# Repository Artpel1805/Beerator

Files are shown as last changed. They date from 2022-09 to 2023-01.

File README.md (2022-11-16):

# <div align="center">Beerator</div>
## Introduction

Le but du projet est de réaliser intégralement un robot capable de se déplacer, de chercher et d’attraper une canette (de bière ? 😶), relever sa couleur, puis de la déposer dans la zone de couleur correspondante.
Partant d’une liste de tous les composants principaux à employer et d’une proposition de châssis, toutes les étapes sont à réaliser de l’aspect matériel (Modélisation sous logiciel de CAO, soudage des composants) jusqu’à l’asservissement logiciel, en passant par la planification et la réalisation du PCB.

Voici un model 3D de ce à quoi pourrais ressembler le robot:

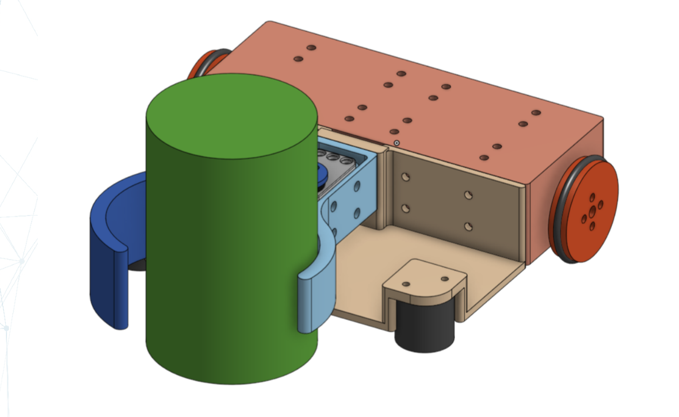
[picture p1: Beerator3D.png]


Le travail fut réparti entre les quatre membres de l’équipe, et les responsabilités suivantes furent attribuées:
* Chef de projet / Responsable intégration : Arthur Pellegrin
* Responsable Software : Nassim Rami
* Responsable Hardware : Adrien Lenoir
* Responsable Livrables : Clarisse Cheng

À l’écriture de ses lignes, nous avons planifié tout le projet, réalisé le PCB, designé et imprimé le châssis. Les composants sont en cours de soudage. Il reste ainsi à réaliser l’assemblage des pièces, l’algorithme de fonctionnement du robot, la commande des différents actionneurs, les calculs d’odométrie, et l’asservissement logiciel.

## General Informations

Vous trouverez dans ce repo bon nombre de dossier.

- Nous avons dans un premier temps rassembler les contraintes et les fonctionnalités du robot dans un cahier des charges: [Cahier des Charges](Cahier%20des%20Charges)

- Nous avons ensuite listé toutes les documentations des composants que nous utiliserons pour répondre à notre cahier des charges dans le dossier [Documentation](Documentation)

- Après cela nous avons architecturer la partie électronique du projet dans le dossier [Diagramme](Diagramme)

- Une fois l'architecture satisfaisante nous avons modéliser la carte électronique sous KiCaD vous trouverez le projet dans le dossier [KiCad/Beerator](KiCad/Beerator). Vous pourrez aussi trouver la BOM dans le fichier

- Nous avons en parallele esssayé d'améliorer le modele 3D du robot. Des choix ont été fait afin d'amméliorer la répartition des masses dans le robots et avoir une meilleure disposition des capteurs.

Les différents travaux effectués sont détaillés dans les parties qui suivent.

## Architecture du projet, schémas fonctionnels

### Architecture de la carte

Pour notre robot, nous proposons l'architecture suivante pour la carte:

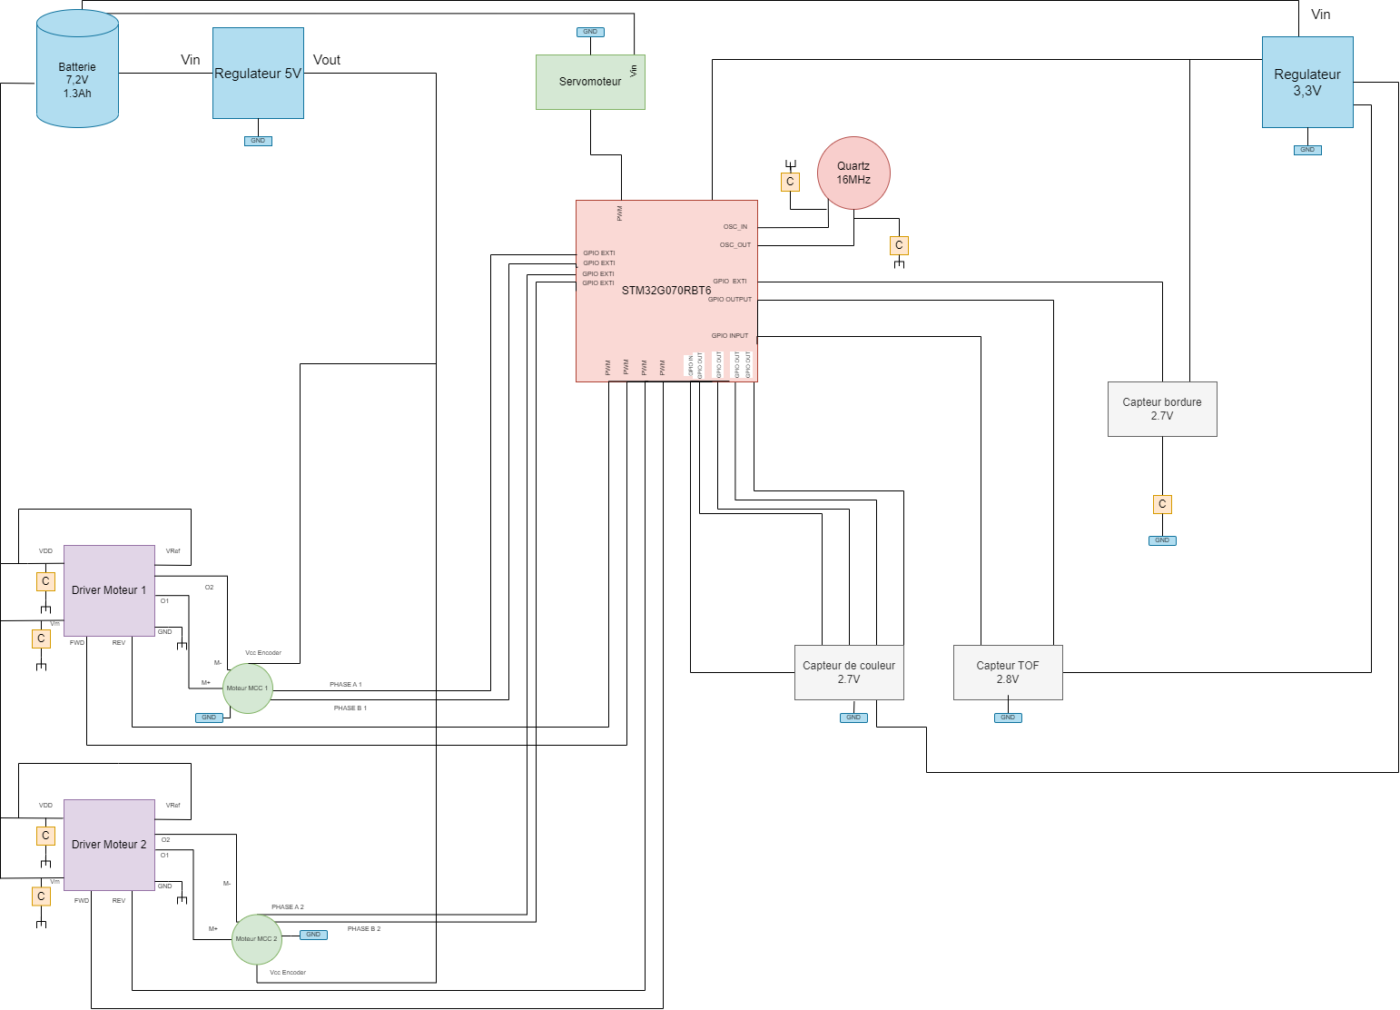
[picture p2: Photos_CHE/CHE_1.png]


Et pour les capteurs:

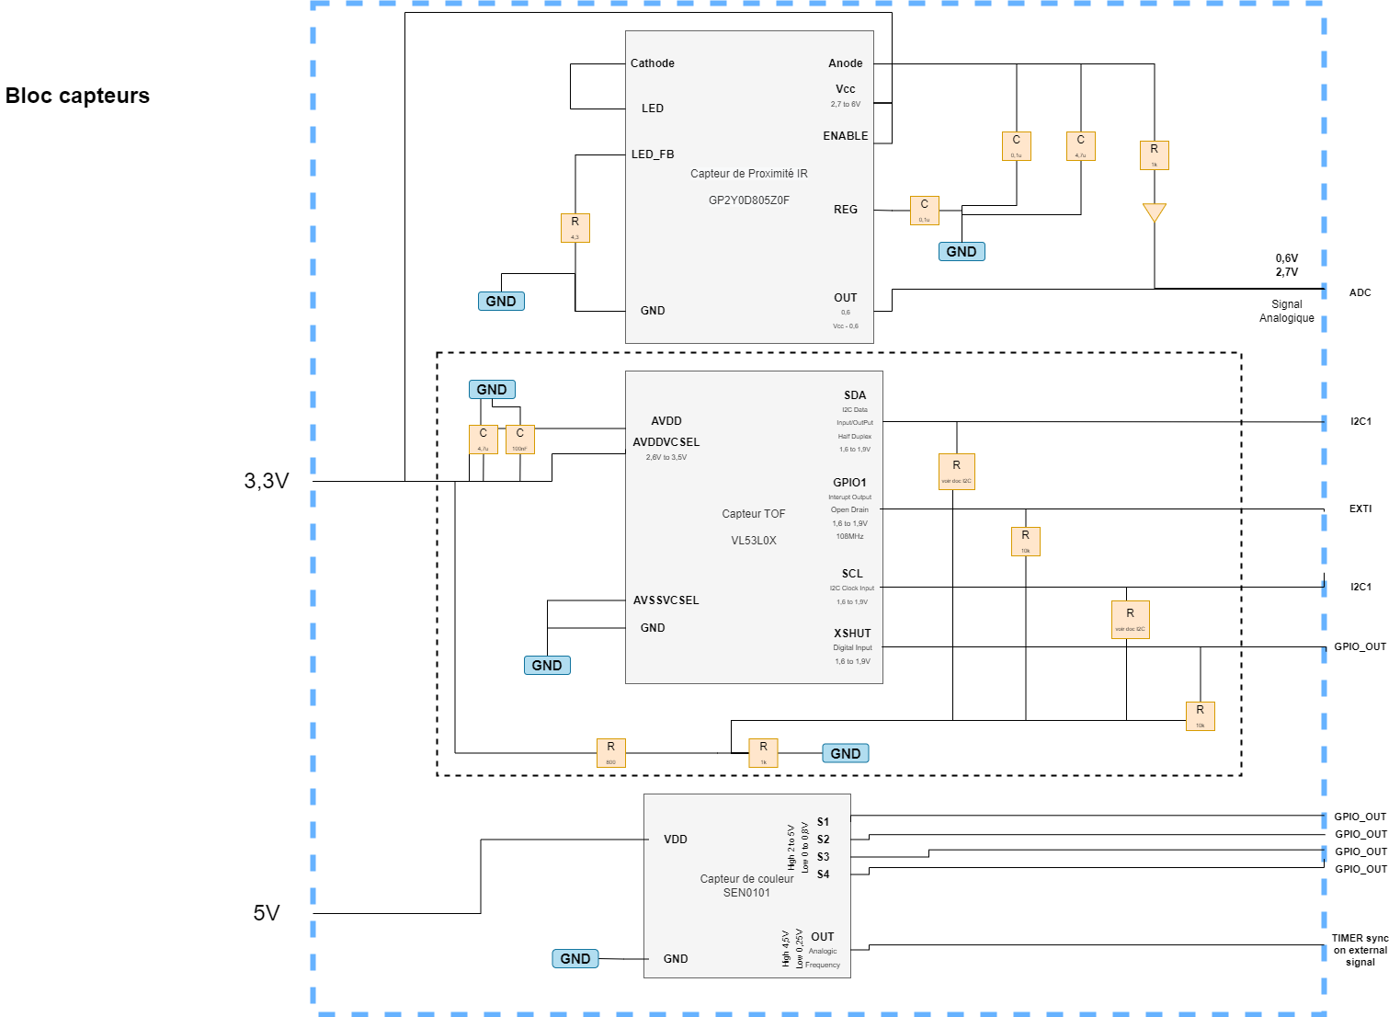
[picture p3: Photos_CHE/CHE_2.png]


* Les deux capteurs IR serviront à détecter les bordures, l’un sera placé à l’avant gauche du robot tandis que l’autre sera à l’avant droit. Ceci évitera au robot de tomber lorsque la distance entre la table et le robot sera supérieur à 5-10 cm environ. Ces deux capteurs IR sont respectivement connectés à une PIN de la STM32, un PIN ADC permettant de recueillir la distance à laquelle se situe la bordure. Le tout étant relié à un régulateur 3.3V permettant de contrôler l’intensité du courant et la tension de sortie.

* Le capteur TOF est connecté à 4 PIN du STM32 avec 2 connexions I2C, 1 EXTI et 1 GPIO OUT. Celui-ci nous permet de connaître la distance à laquelle se situent les canettes.

* Le capteur de couleur est équipé d'un oscillateur interne, oscillateur qui produit une onde carrée dont la fréquence est proportionnelle à l'intensité de la couleur. Fréquence qui nous permettra de déterminer la couleur de la canette. Ce capteur de couleur a une portée très, c’est pour cela que nous l’avons placer au creu de la pince.

* Quatre PWM seront utilisés pour contrôler le hacheur droit et gauche des moteurs

### Architecture de l’alimentation

Voici l’architecture de l’alimentation:

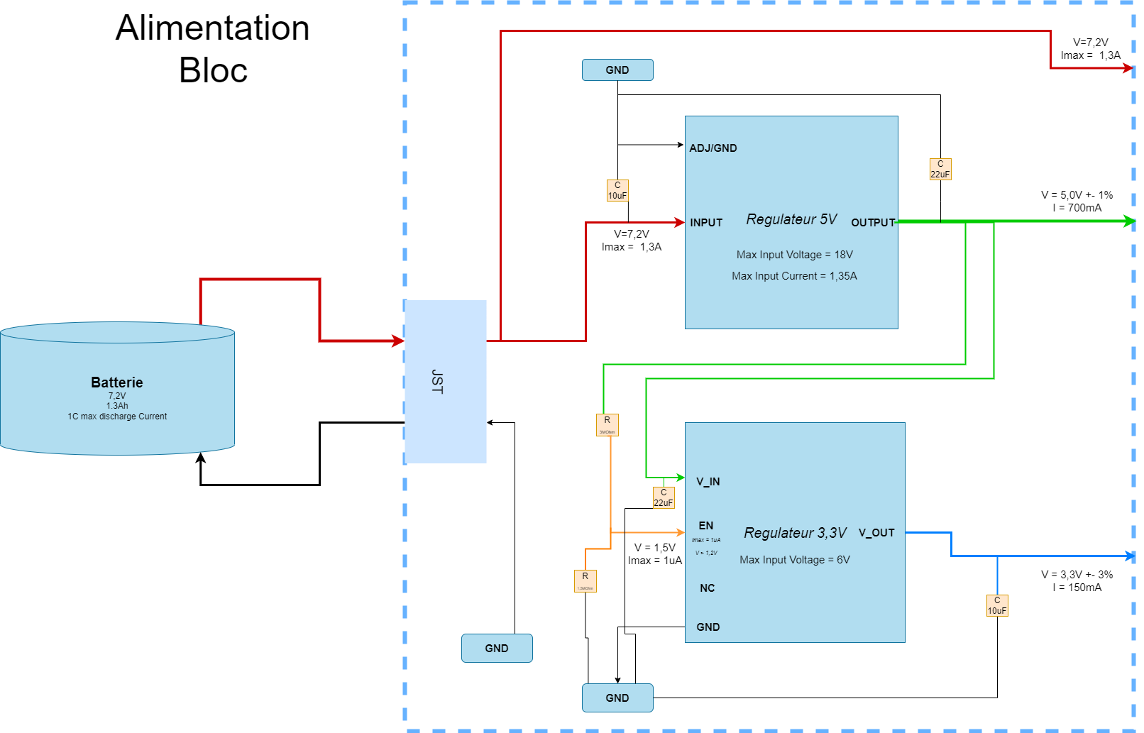
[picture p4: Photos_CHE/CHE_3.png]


Dans un premier temps, la batterie de 7.2V va nous permettre d’alimenter nos différents régulateurs qui vont à leur tour alimenter les composants de notre robot.

Les capteurs TOF et IR ont besoin d’une tension de maximale de 2.8V, on utilise donc un régulateur 3.3V pour abaisser la tension de l’alimentation. 
De même, pour le capteur de couleur, nous utilisons un régulateur 5V.

### Diagramme d’état

Voici le diagramme d’état du robot qui spécifie les réactions du robots à différents évènements qui pourraient avoir lieu. Le but du robot est d'abord de détecter la canette ou les canettes présente sur la table, pour se diriger vers elle, la saisir puis la déposer dans la zone qui correspond à sa couleur. Ces étapes sont développées dans le diagramme d’état ci-contre.

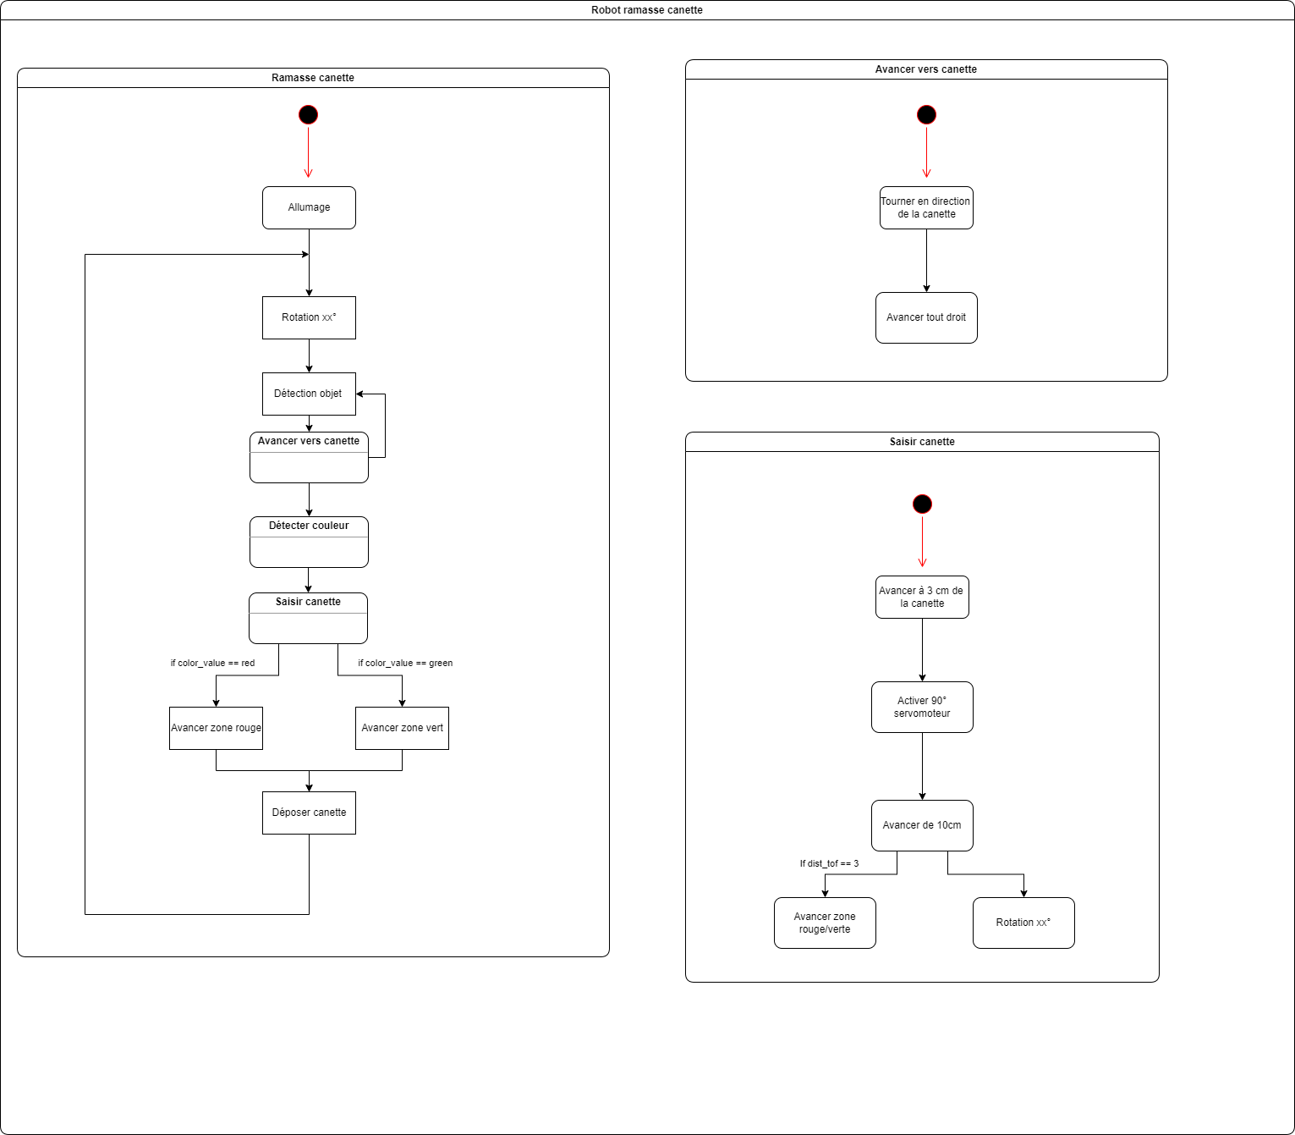
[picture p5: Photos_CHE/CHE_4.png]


## Planification du circuit, Création du PCB

Comme vu précédemment nous avons découpé l'électronique de notre robot en 4 blocs fonctionnels.

Nous devons maintenant créer le schéma électronique de notre carte en respectant cette répartition. Cela n’a pas d'effet sur l'électronique impliqué, mais cela aidera à la maintenabilité et à la lisibilité du projet.

De même, nous traitons chaque composant indépendamment. Ils seront reliés grâce à des labels dans le logiciel * KiCad *.

### ALIMENTATION

Nous avons décidé de connecter la batterie grâce à un JST, ainsi nous pourrons facilement la retirer pour la recharger.
Concernant les régulateurs, nous dimensionnons leurs capacités de découplage en accord avec leurs documentations respectives.

Nous avons ensuite décidé de rajouter des témoins d’alimentation sur la batterie et le 3.3V. Les leds que nous avons choisies consomment 10mA pour fournir une luminosité maximale.
Comme ce sont uniquement des témoins (Nous n’avons pas besoin de beaucoup de luminosité) et que le 3.3V ne peut pas fournir une trop grande intensité nous avons choisis de réduire le courant maximal à 1mA. 
Nous dimensionnons donc les résistances en conséquence, avec une loi d’ohm sachant que les LEDs sont en 3V. 

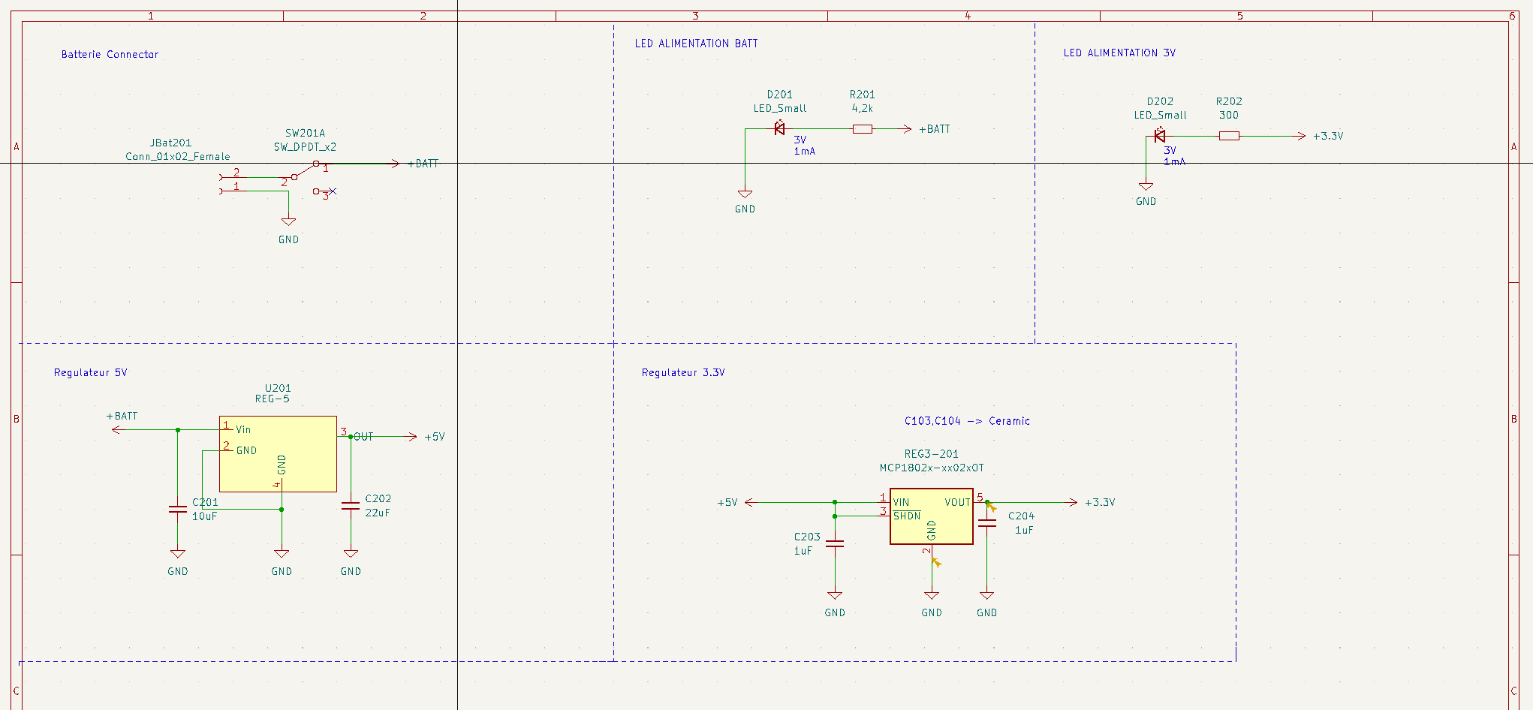
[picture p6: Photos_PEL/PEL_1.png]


### CAPTEURS

Nous avons décidé de connecter tous nos capteurs grâce à des JST. 
Cela permettra une meilleure modularité physique des capteurs sur le robot.
Cela évite aussi de concevoir une grande carte ou plusieurs cartes, les capteurs disposant presque tous de leur propre carte.

Nous avons quand même dû ici respecter la géométrie des capteurs afin que les JST correspondent aux bonnes I/O des cartes électroniques des capteurs.

Des résistances de Pull-Up ont dû être ajoutées, pour l’I2C car cela est nécessaire pour que ce protocole fonctionne correctement.

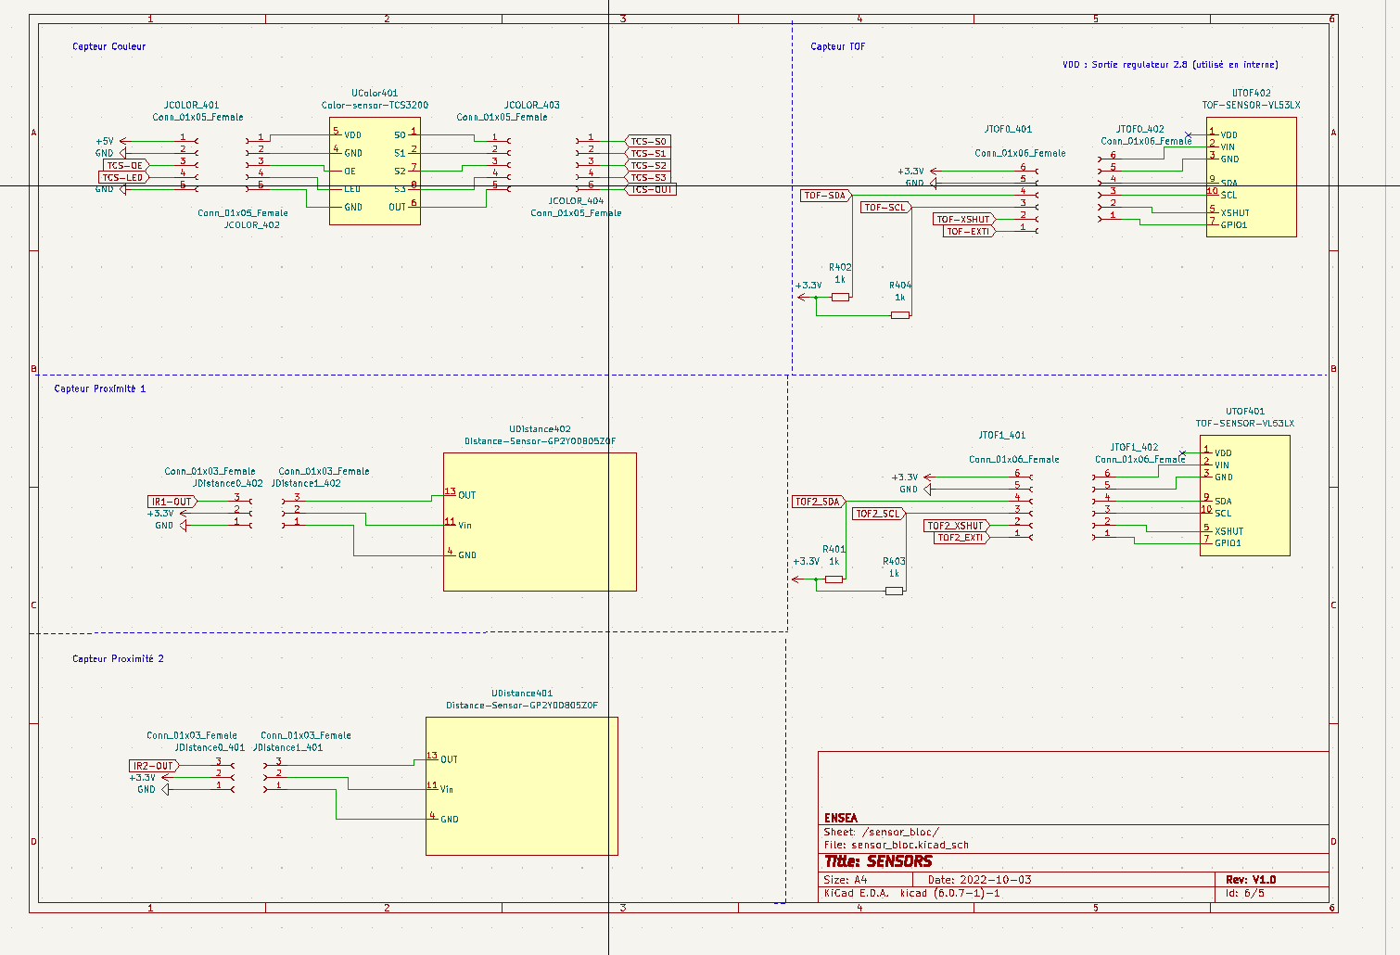
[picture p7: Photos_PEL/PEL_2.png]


### ACTIONNEURS

Nous avons 3 actionneurs - 2 MCC et 1 Servomoteur.

Les MCC sont commandés par des Drivers et leurs capacités de découplage.
Cette partie du projet est assez délicate. Nous décidons donc de mettre des Solder Jump afin de pouvoir tester nos signaux avant de les connecter aux moteurs.

Le Servo quant à lui suit un protocole particulier, il sera branché sur un port USART en mode Half-Duplex du uP nécessitant une résistance de Pull-Up.

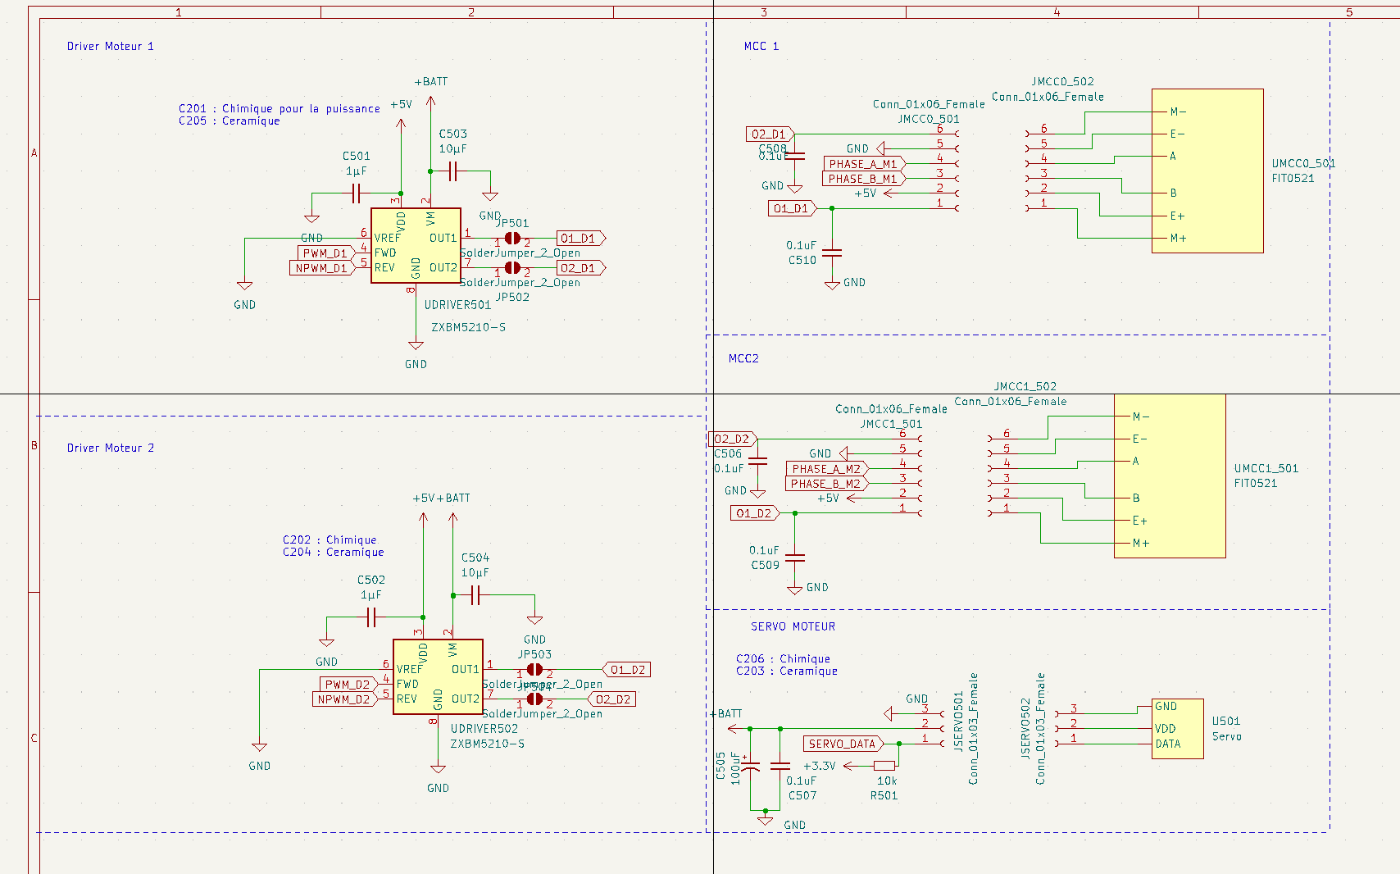
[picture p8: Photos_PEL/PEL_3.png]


### CONTRÔLEUR

Jusqu’ici tous les modèles électroniques et les placements de toutes les I/O étaient imposés par les constructeurs.

Nous modélisons le microcontrôleur avec ses 64 broches. 
Ensuite nous avons dû brancher tous nos composants à notre microcontrôleur.

Nous avons mis un point d’honneur à optimiser le choix des broches en suivant un protocole bien particulier: 
Regrouper au maximum les broches étant reliées à un même composant
Organiser les broches de manière à minimiser les croisements lors du routage
Segmenter les sous-circuits
Prendre en compte les problèmes de compatibilité électgromagnétique

Grâce au logiciel STM32CubeMx nous avons pu placer les broches sur des pins répondant aux besoins.

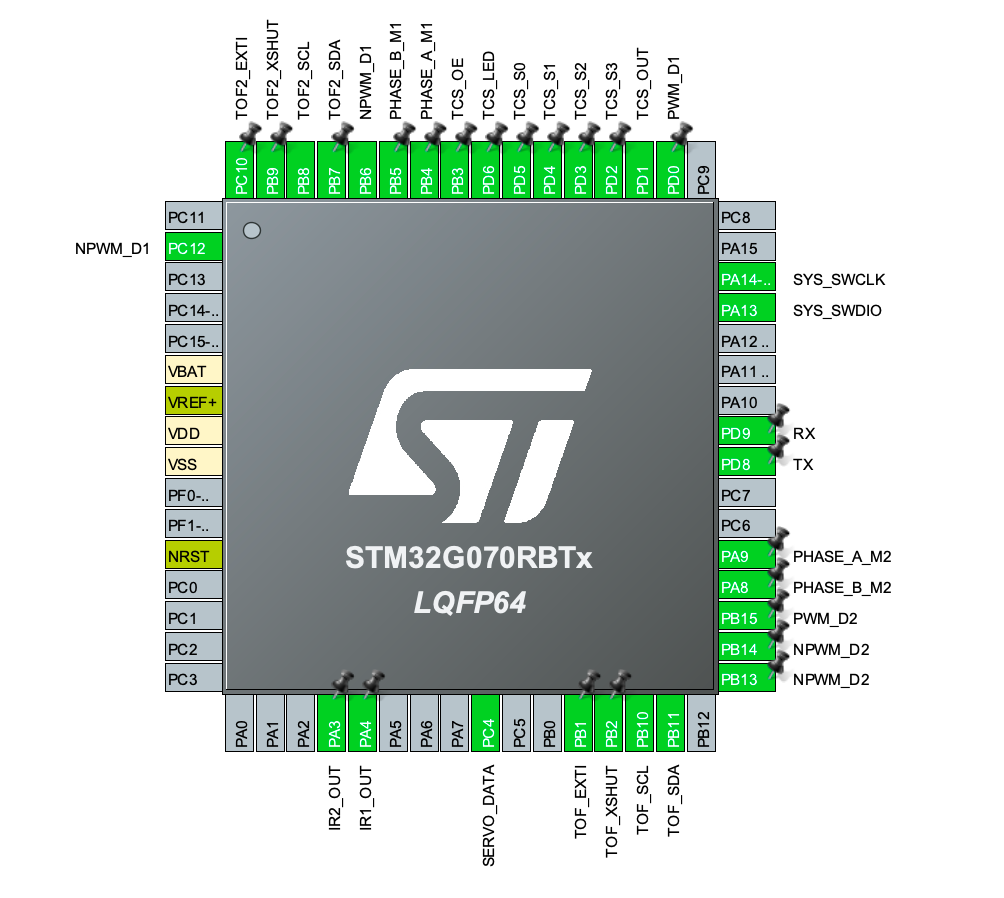
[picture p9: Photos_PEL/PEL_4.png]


Nous devons aussi alimenter le STM32 et il ne faut surtout pas oublier les capacités de découplage car l’alimentation doit être la plus stable possible.

Nous choisissons aussi de rajouter un Quartz externe, car l’horloge est plus précise.

Il ne faut pas oublier de rajouter, les branchements pour le STLink car c’est lui qui nous permettra de programmer le STM32.

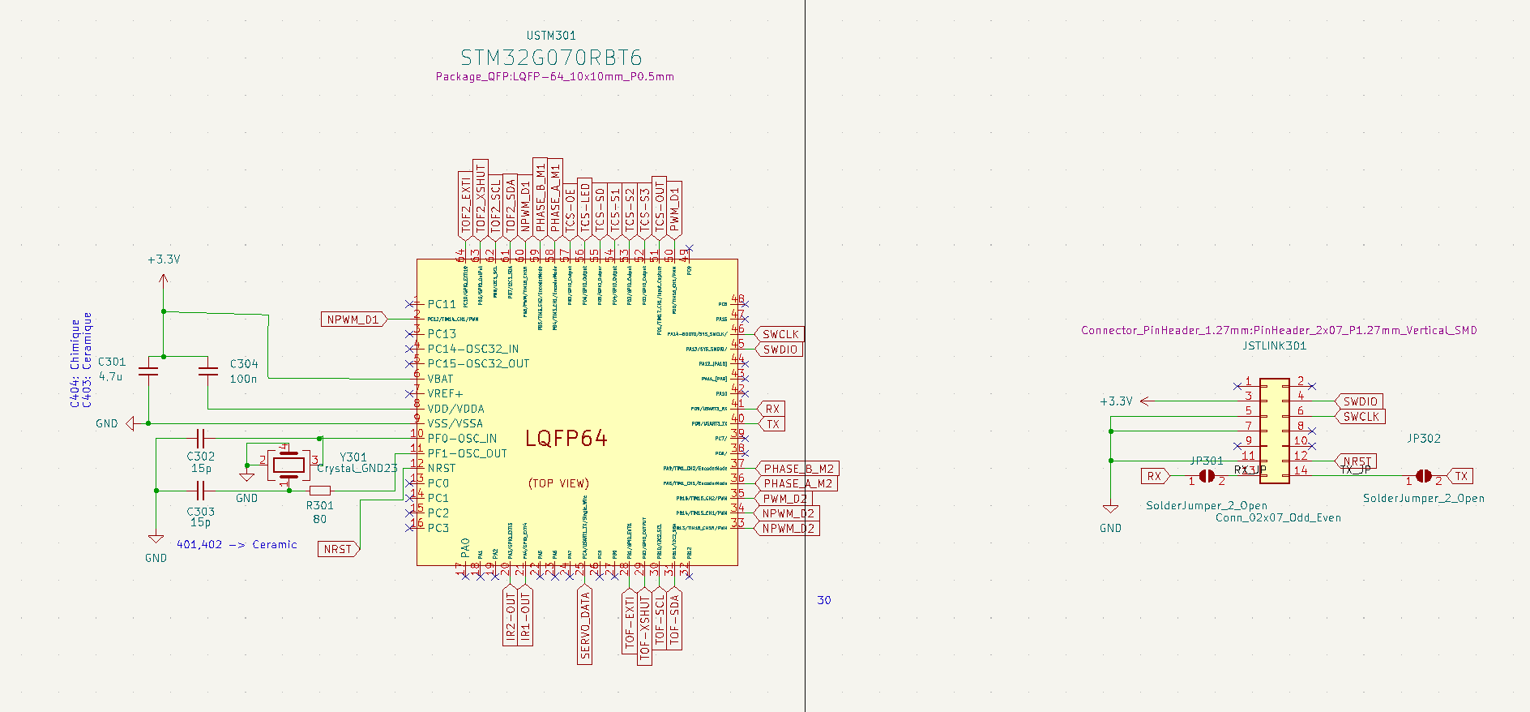
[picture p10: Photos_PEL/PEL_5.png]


Enfin nous réalisons une analyse électrique de notre circuit pour savoir s’il comporte des erreurs et nous les corrigeons jusqu’à ce qu’il n’y en ai plus.

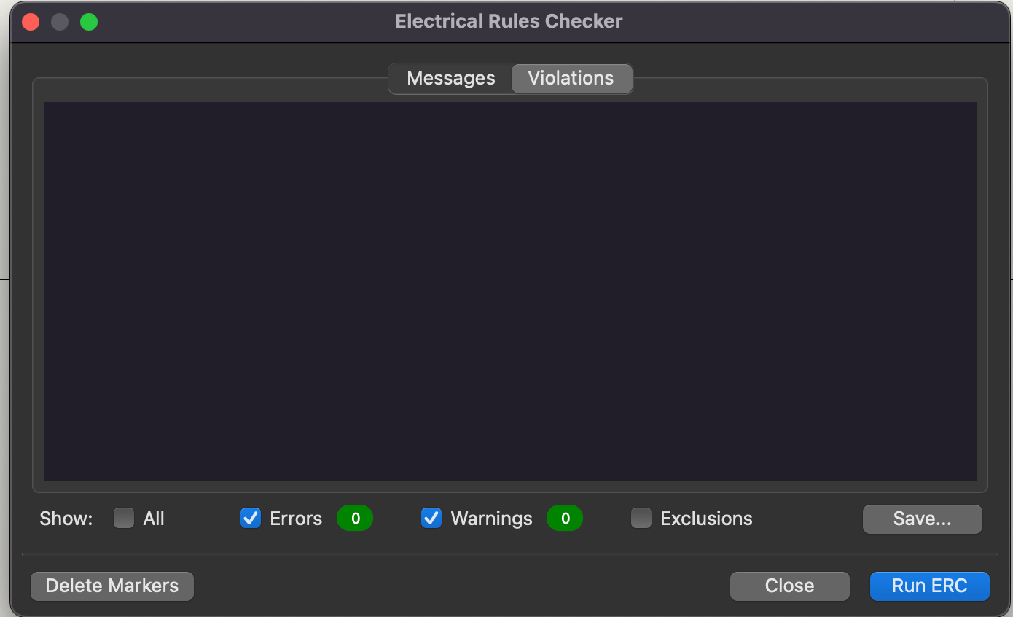
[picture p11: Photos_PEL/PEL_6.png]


### Production du PCB

La prochaine étape est d’assigner les empreintes correspondants aux composants. Nous utiliserons des composants SMD 0603. Pour les connecteurs nous avons utilisé des connecteurs JST de type JST HX 2.54mm.
On peut remarquer que certains composants ne sont pas assignés, en effet ce sont les composants qui seront directement soudé au capteur donc ils ne doivent pas être présent sur notre PCB

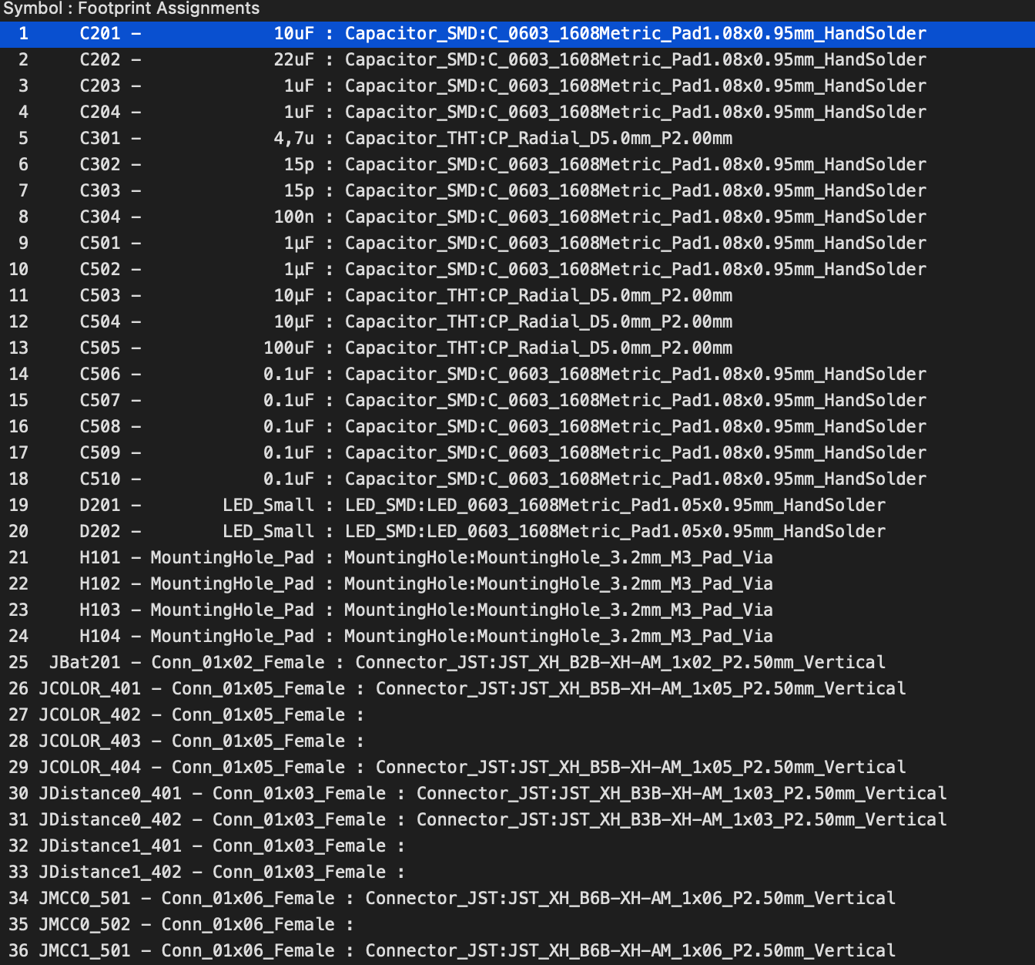
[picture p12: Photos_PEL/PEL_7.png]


Nous travaillons sur un PCB 4 couches, on décide donc d’y placer 2 plans de potentiels séparés par 2 plans de masses pour d'obscures raisons de CEM.
On peut voir ci dessous le Stack-Up de notre carte

* <font color=red>5V (Rouge)</font>
* <font color=green>GND (Vert)</font>
* <font color=yellow>3,3V (Jaune)</font>
* <font color=blue>GND (Bleu)</font>

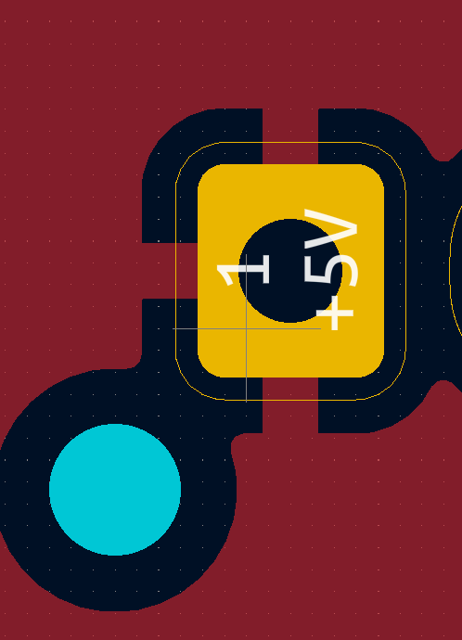
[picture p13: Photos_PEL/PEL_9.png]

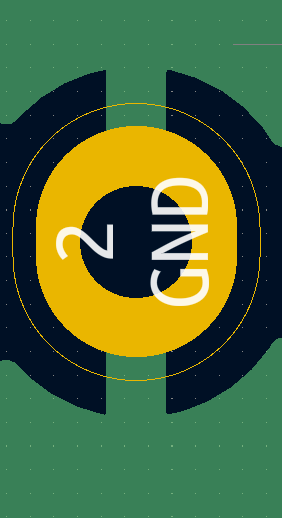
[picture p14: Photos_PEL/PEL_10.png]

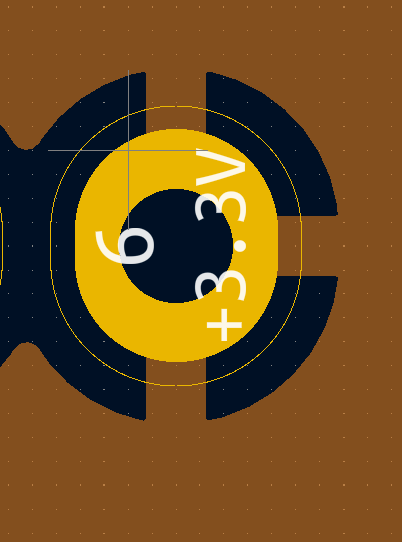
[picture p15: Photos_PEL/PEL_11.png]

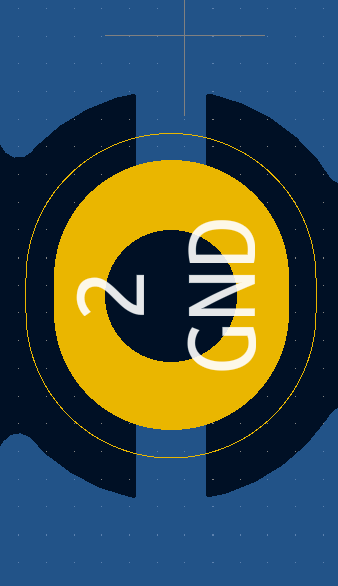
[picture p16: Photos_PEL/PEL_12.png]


JLC PCB, le fabricant de nos carte nous impose aussi des contraintes de conception que nous devons renseigner.

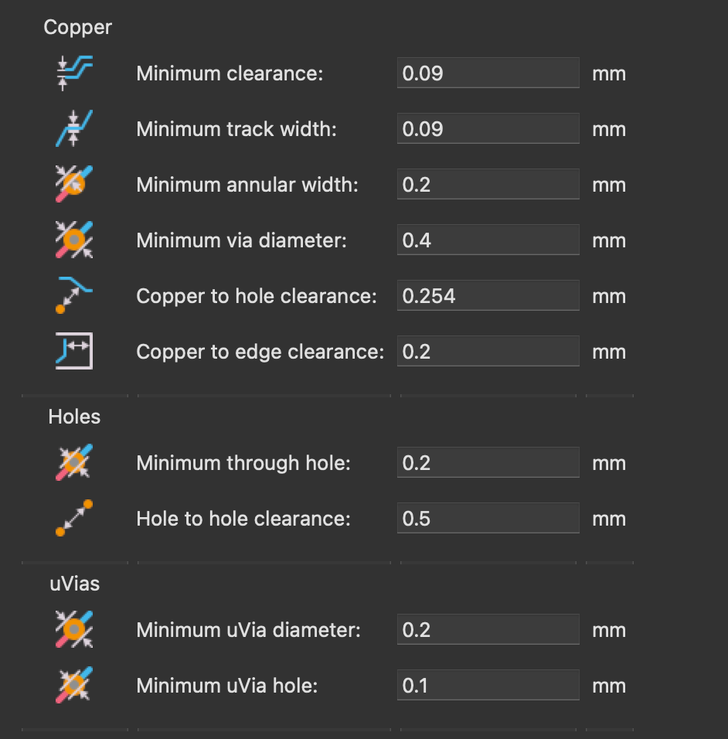
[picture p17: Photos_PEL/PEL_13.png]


La prochaine est le placement des composants sur le PCB.
Nous essayons de regrouper les composants au maximum par groupe pour que le routage soit le plus simple possible

On décide aussi de placer le STM32 au centre car c’est lui qui possède le plus de connexion.

On voit ci dessous en vert tous les composants relatif au contrôle, en rouge tous le bloc actionneurs, en bleu le bloc alimentation et en jaune le bloc capteur

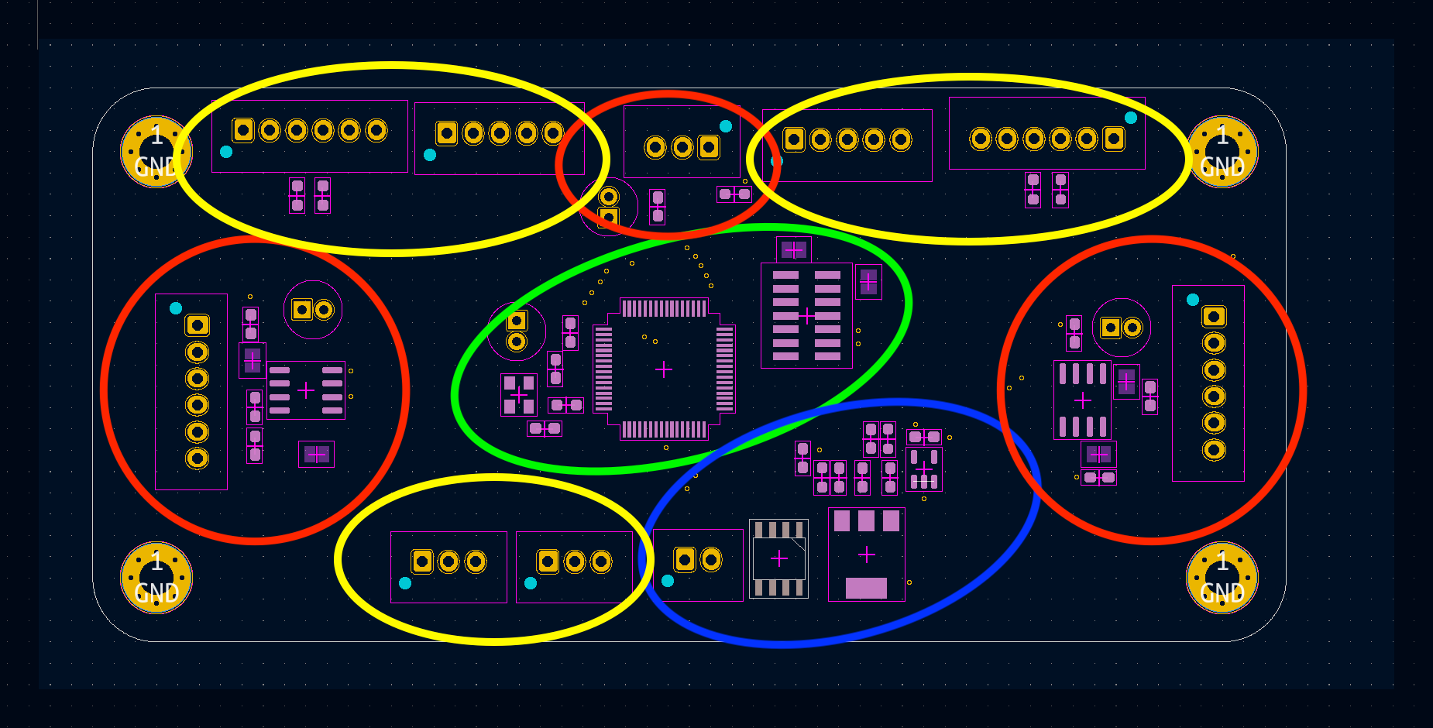
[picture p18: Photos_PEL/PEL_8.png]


Nous relions ensuite tous les composants électriquement. Nous veillerons aussi à utiliser les pistes les plus larges possible surtout pour la partie puissance. 
Cela permet de laisser passer le courant nécessaire et d’éviter des problèmes de CEM.

Quelques règles de CEM que nous nous efforçons de respecter : 
Pas d’angle à 90º
Les signaux à haute fréquence ne doivent pas se croiser, et les pistes doivent être le plus court possible
Il faut essayer de respecter une distance entre les pistes

Voici ce à quoi ressemblent nos deux plans avec des pistes.

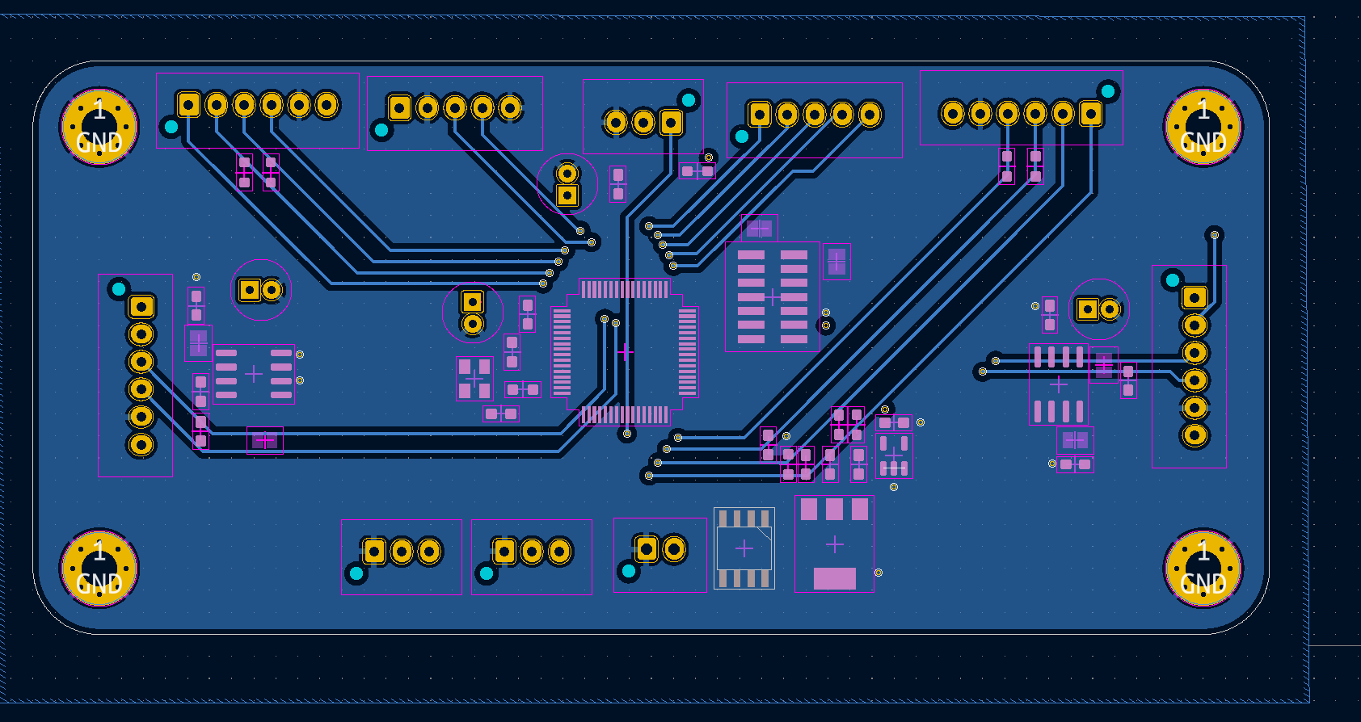
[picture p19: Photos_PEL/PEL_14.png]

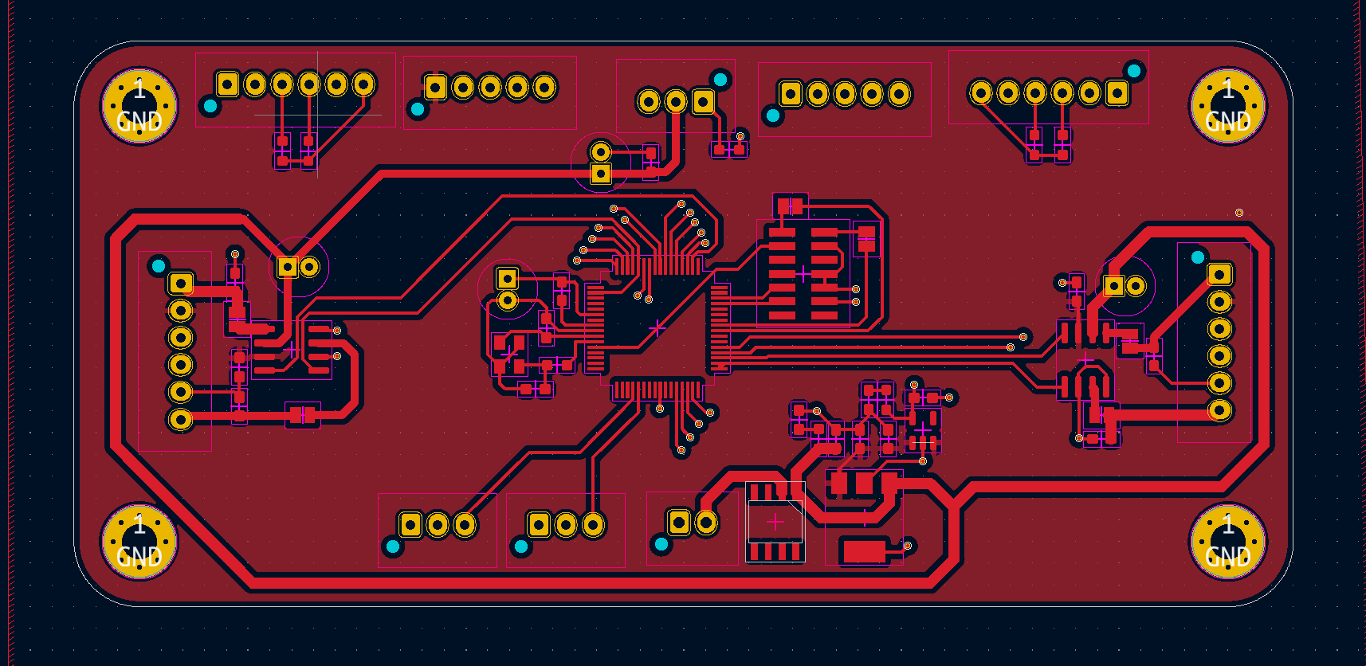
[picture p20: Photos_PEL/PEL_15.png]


Et enfin notre carte modélisé en 3D

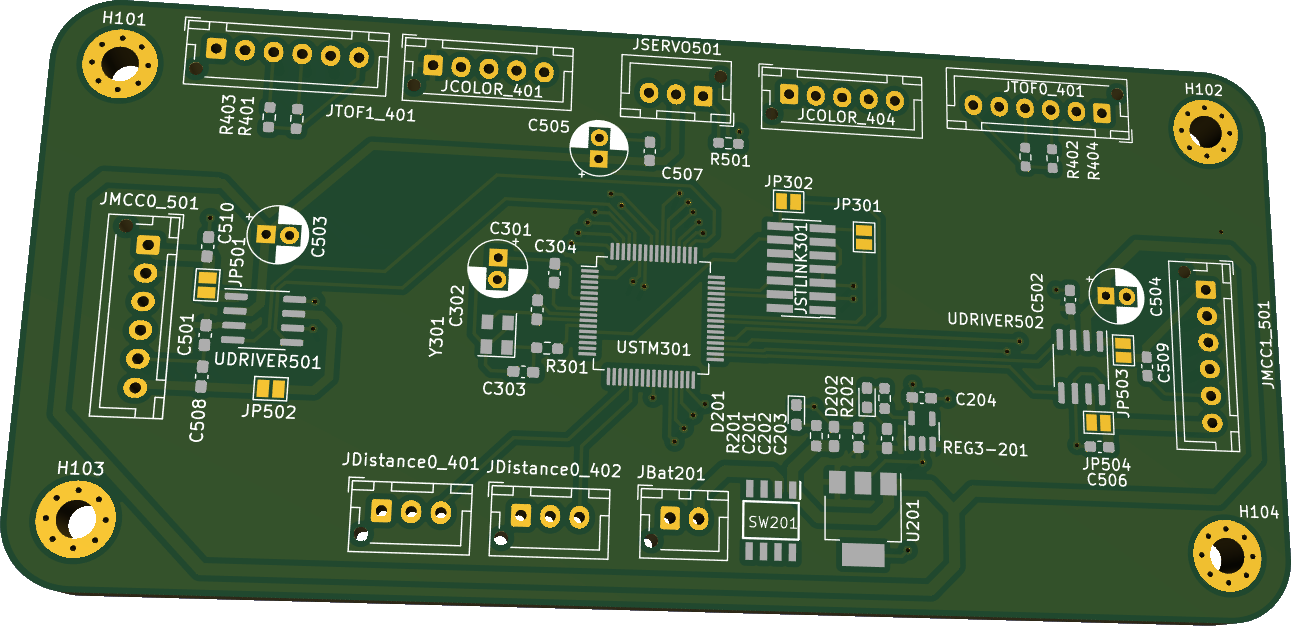
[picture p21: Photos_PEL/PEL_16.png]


## Capteurs, spécificités software

Dans cette partie, on se basera sur le choix des composants et leur protocole de communication ainsi que leur fonctionnalité pour atteindre les objectifs demandés par le cahier de charge afin que le robot puisse fonctionner correctement.

### TCS3200 - Capteur de Couleur

Le capteur VEML3328 détecte les couleurs rouge, le vert, le bleu en incorporant des photodiodes, des amplificateurs et des circuits analogiques/numériques dans une seule puce CMOS. Avec ce capteur, la luminosité et la température de couleur d'un rétroéclairage d'affichage peuvent être ajusté en fonction de la source de lumière ambiante, et il peutdifférencier les environnements d'éclairage intérieurs des environnements d'éclairage extérieurs.Il existe une relation entre la sortie et l'intensité lumineuse. La gamme de  sortie est typique de 2hz à 500Khz.
Ce dispositif utilise une liaison direct avec le microcontrôleur.
Puisque le diapositif nous fournit comme output un signal variant en fréquence , on a utilisé la fonction du Timer : Input capture mode , qui permet de détecter chaque front montant et en calculant la différence on peut avoir la fréquence.

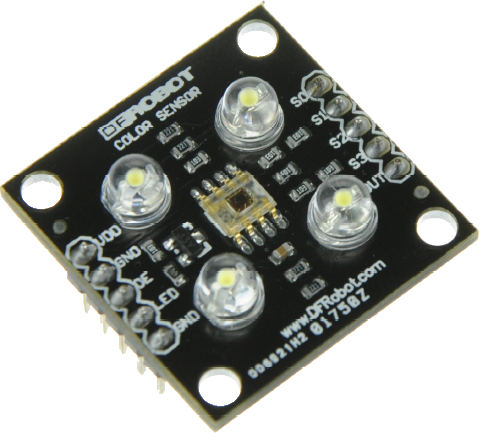
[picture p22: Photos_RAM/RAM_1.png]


#### Calibration

Pour calibrer le capteur, nous avons besoin d'un objet blanc.On place un objet blanc près du capteur. Après le calibrage, si on garde l'objet blanc devant le capteur, on voit la valeur de 255 pour chacune des trois couleurs rouge, verte et bleue. La fonction Calibrate puis on crée une fonction Calibrate() qui  calcule et stocke les changements maximum et minimum de la fréquence de sortie du capteur dans un environnement non coloré et de couleur blanche. Ensuite,on mappe la plage de changement de couleur sur 0-255 .

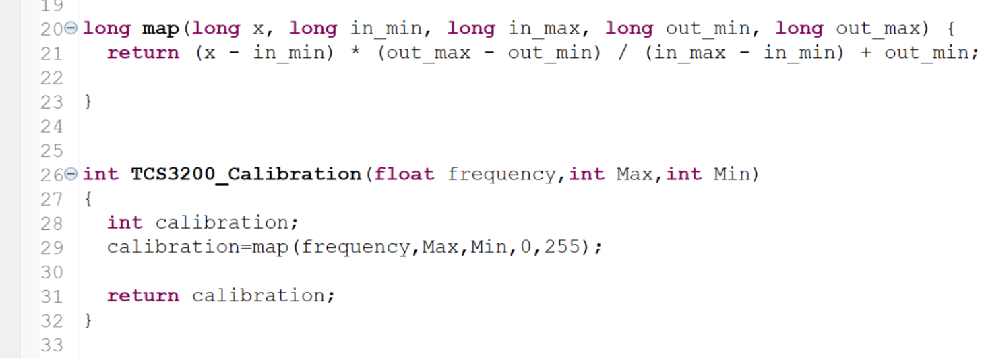
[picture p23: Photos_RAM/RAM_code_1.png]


Le dispositif dispose de deux broches en changeant leur état permet de choisir la couleur qu’on veut détecter en faisant appel la fonction Calibration() à chaque interruption.

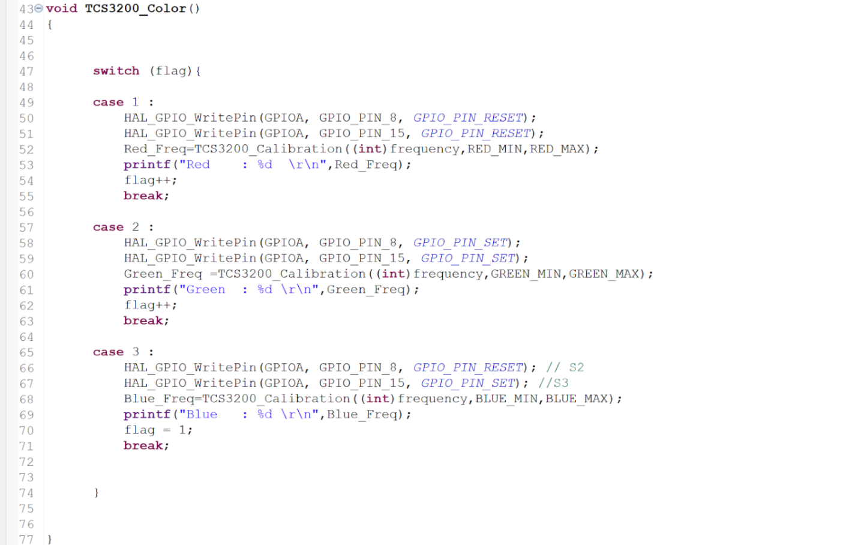
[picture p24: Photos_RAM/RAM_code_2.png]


Le capteur nous fournit un signal carré comme sortie variant en fréquence en fonction de la distance entre l’objet et le capteur  , c’est pour cela qu' on a utilisé la fonction Input Capture Mode du Timer qui permet de détecter chaque front montant . 
En utilisant cette fonctionnalité , on pourra calculer la fréquence en calculant la différence entre deux fronts montants et l'horloge de référence est calculée en fonction de la configuration que nous avons effectuée . puis en disant l’horloge de référence par la différence précédente.

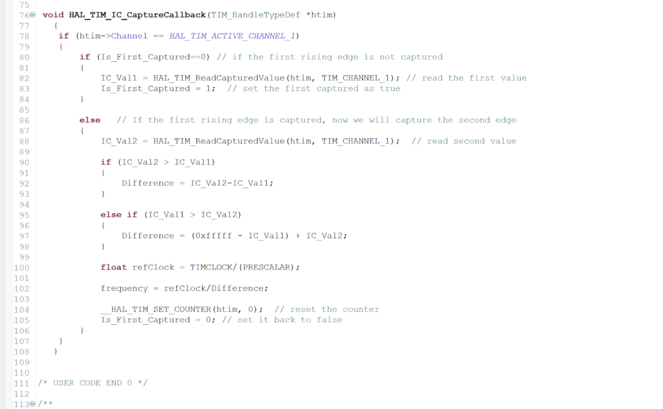
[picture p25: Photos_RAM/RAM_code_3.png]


### VL53L0X - Capteur de distance TOF

Il s'agit d'un capteur ToF (Time-of-Flight), c'est-à-dire que la distance est mesurée en mesurant le temps de vol. Le capteur vérifie combien de temps il faut à la lumière pour atteindre l'objet, rebondir dessus et revenir au capteur de réception (Réflexion). Le capteur communique avec l'hôte via l'interface I²C. Outre les broches de bus standard, une sortie d'interruption et une entrée pour l'arrêt du capteur sont également disponibles.

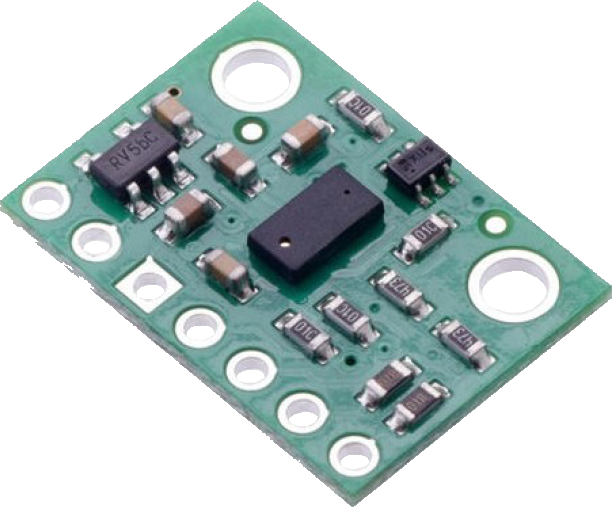
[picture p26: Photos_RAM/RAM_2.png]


#### Programmation

ST ajoute une bibliothèque complète au capteur  Elle contient tout ce qui peut être fait avec le système.
On a testé la bibliothèque pour extraire les données du capteur sauf que la bibliothèque est universellement écrite et  elle prend donc beaucoup de code,ce qui représente beaucoup de mémoire Flash.
Pour cela on est obligé de créer notre propre drivers pour extraire les données et communiquer avec le capteur.

### Sharp GP2Y0D805Z0F - Capteur de Proximité Infrarouge

Ce capteur de proximité infrarouge de Pololu permet de détecter sans contact tout objet entre 0,5 et 5 cm . Sur la carte électronique,on retrouve 3 broches : la pastille carrée est la masse, la pastille du milieu est l'alimentation Vin (entre 2.7 et 6.2 V) et la dernière pastille est la sortie du capteur de proximité infrarouge.On peut améliorer la performance du capteur en plaçant une capacité (>10uF) entre l'alimentation et la masse.

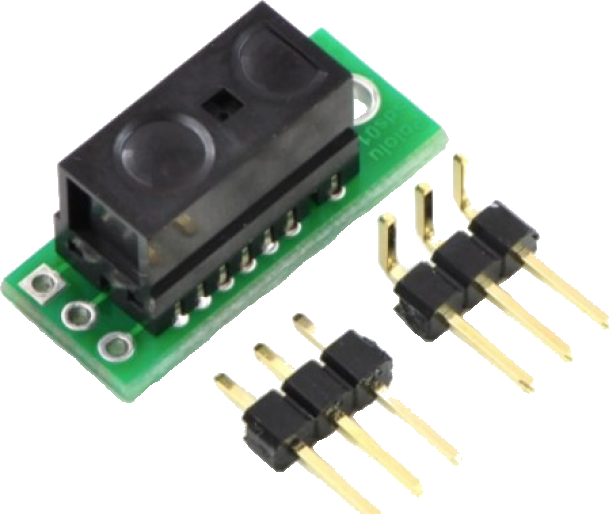
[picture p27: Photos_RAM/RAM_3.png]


## Architecture matérielle, Modélisation

### Généralités

Afin de pouvoir intégrer les éléments imposés du projet sur le robot, nous avons dû modéliser un châssis qui reprend la forme proposée en incluant les capteurs. Pour maximiser la fiabilité de ce robot en termes de trajectoire et faciliter sa commande/son asservissement, nous avons voulu modifier sa géométrie en plaçant entre autres son centre de gravité en aval de son centre de poussée (pour la marche avant), et en rendant quasi parfaitement symétrique el robot, que sa pince soit ouverte ou fermée. Ainsi les batteries se retrouvent à l’arrière, les moteurs contrôlent la rotation des roues directement à l’avant, le troisième point d'appui omni-directionnel est juste derrière les batteries, et la pince à l’opposé, tout à l’avant en porte à faux. Elle opère en un mouvement synchronisé de trois mords qui serrent et soulèvent légèrement du sol la canette interceptée, grâce à une légère inclinaison du système, comme on peut le voir ci-dessous.

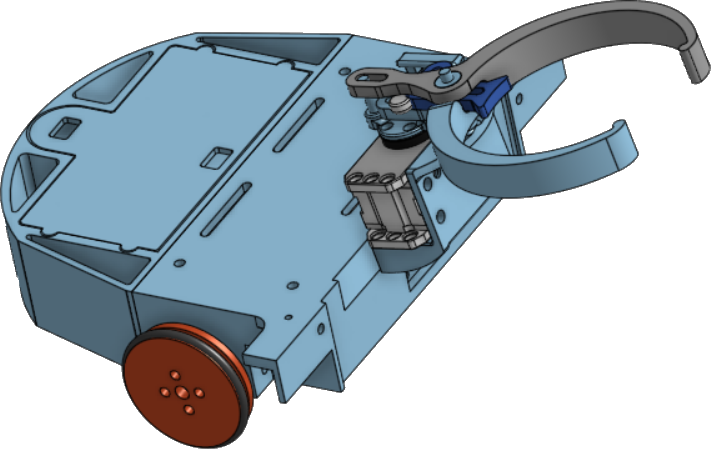
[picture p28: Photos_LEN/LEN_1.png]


Le tout confère au robot une allure de scorpion.

### Placement des capteurs

Les deux capteurs infrarouges anti-chute sont situés sur les côtés, juste devant les roues, de façon à toujours détecter la chute potentielle à temps et à pouvoir faire revenir le robot sur ses pas si nécessaire.

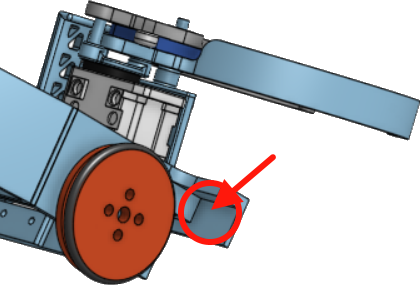
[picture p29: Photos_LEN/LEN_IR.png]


Le capteur de couleur est placé juste sous la pince, avec la même orientation, afin de lire au plus proche la couleur de la canette saisie, car ce type de capteur ne fonctionne pas de façon fiable au delà d’une distance de quelques centimètres.

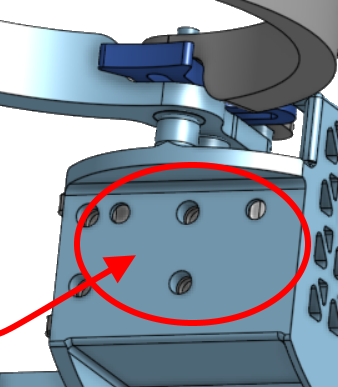
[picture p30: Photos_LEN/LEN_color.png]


Le capteur de distance ‘TOF’ est quant à lui placé sur un plan vertical, sur le front du robot, afin de lire sans obstruction la distance avec les obstacles/cibles rencontré(e)s.

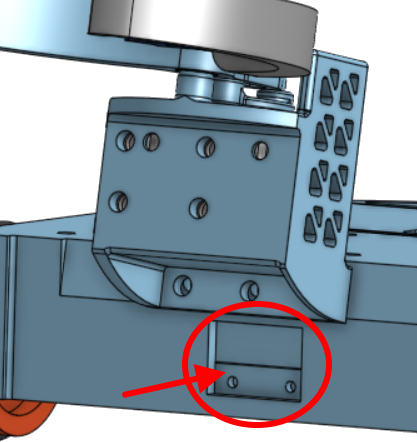
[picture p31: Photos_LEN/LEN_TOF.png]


### Dimensions des pièces

Les capteurs et actionneurs utilisés par le robot sont à l’origine de sa géométrie, et dans le souci de bâtir un modèle correspondant au mieux aux critères énoncés plus haut, il fallait à présent recenser les dimensions physiques de chaque élément. Ce recueil apparaît ci-après.

* Canette (33 cL standard) | Ø: 66 mm, H: 115 mm
* Canette (50 cL standard) | Ø: 66 mm, H: 168 mm
* Batterie (avec assez de marge pour les fils) | l: 48 mm; L: 95 mm; H: 15 mm
* Moteurs avec codeur (sans l’axe) | Ø: 25 mm, L: 59 mm
* Servomoteur (pris aux centres des points de fixation) | l: 24 mm; L: 18 mm; H: 12 mm
* Capteur IR | l: 8.9 mm; L: 21.6 mm; H: xx mm
* Capteur de couleurs | l: 28.4 mm; L: 28.4 mm; H: xx mm
* Capteur TOF | l: 12.7 mm; L: 17.8 mm; H: xx mm
* PCB (pris aux centres des points de fixation) | l: 40 mm; L: 100 mm
* Bille (Roulement omnidirectionnel) | Ø: 22.9 mm, H: 20.9 mm
* Roues avec support | Ø: 40 mm, H: 8 mm

### Cable management

Tous les câbles parcourent le chemin le plus court pour parvenir à la carte, en s'immisçant dans des sillons et fentes prévus à cet effet dans le châssis.

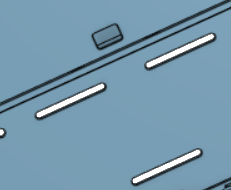
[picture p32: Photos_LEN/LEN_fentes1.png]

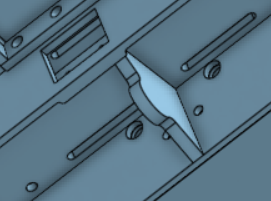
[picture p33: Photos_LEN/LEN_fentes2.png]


Ainsi on évite les erreurs de branchement, les croisement et les fils trop exposés.

### Le système de pince

Comme expliqué plus haut, la pince s’articule en trois mords synchronisés, deux maintiennent la canette, le troisième la soulève.

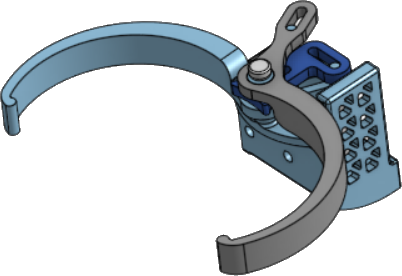
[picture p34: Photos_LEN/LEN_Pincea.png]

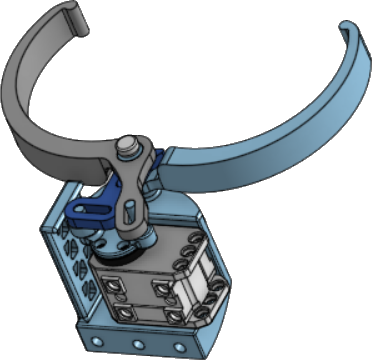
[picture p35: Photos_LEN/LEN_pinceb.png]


Le servomoteur fait passer la pince entre ses états fermés et ouverts sur une course de 90°. Deux mouvements proches mais opposés en sens ferment les deux crochets de pince arrondis, pendant que la troisième composante de la pince s’avance pour refermer l’emprise du robot sur sa bière et la soulever légèrement du sol, pour la vider pour ne pas qu’elle frotte. Cela peut paraître superflu, mais peut jouer un rôle important sur une surface non plane ou rugueuse.

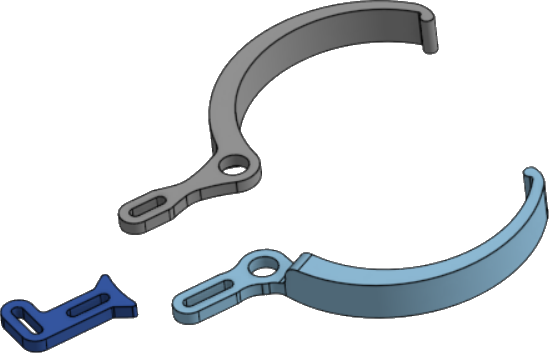
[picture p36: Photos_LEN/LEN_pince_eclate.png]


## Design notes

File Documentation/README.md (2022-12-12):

**Servo**
https://emanual.robotis.com/docs/en/dxl/x/xl320/

## Driver Moteur

PWM Frequency for input voltage 7,2V => 26,5kHz
64Mhz => ARR = 240 , PSC=9

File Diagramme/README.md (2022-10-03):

# Diagrams

## Bloc Diagram

Nous avons décidé dans un premier temps de schématiser la partie électronique du projet grâce à une architecture très générale. Nous avons décider de découper le projet en 4 grands Blocs:

- L'alimentation : Ce Bloc va être en charge de fournir de l'énergie à tous les composants de notre robot
- Les capteurs : Ce BloC va être en charge de récolter des données sur l'environement de notre robot
- Les actionneurs : Ce Bloc est responsable de tous les mouvements de notre robot
- Le contrôleur : C'est le cerveau du robot, c'est lui qui permet au robot d'atteindre son objectif 

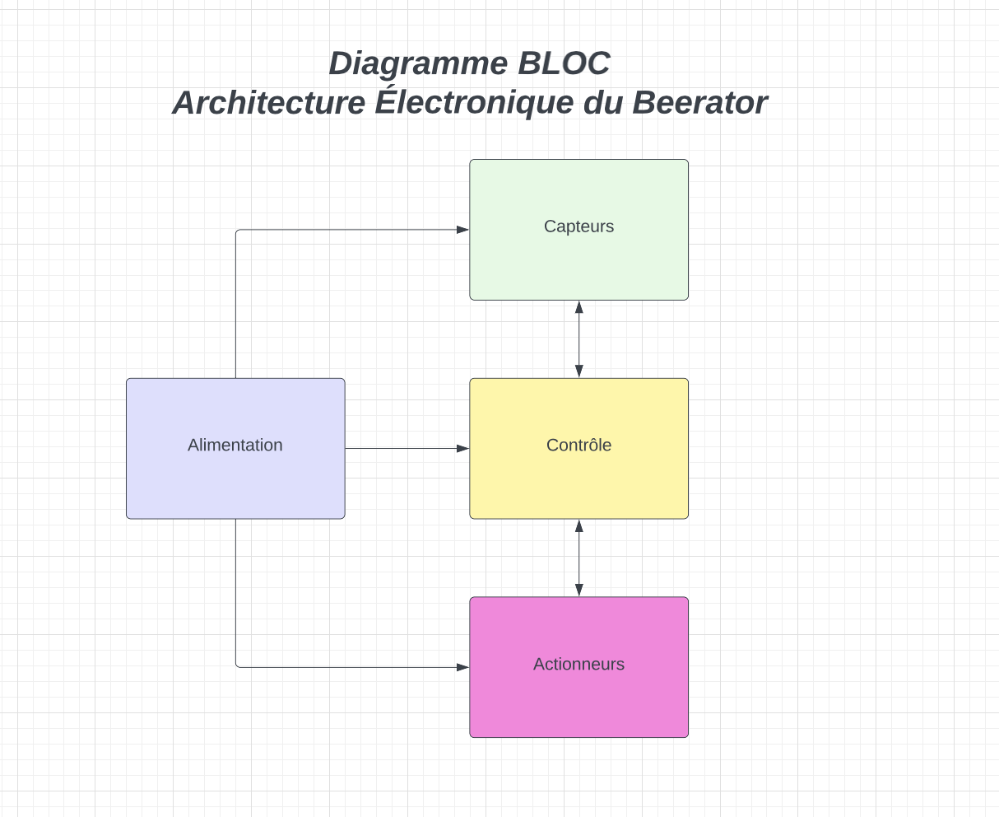
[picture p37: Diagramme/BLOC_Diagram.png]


## Technical Diagram

Détaillons maintenant chaque Bloc de manière plus technique

### L'alimentation

### Les capteurs

### Les actionneurs

### Le contrôleur

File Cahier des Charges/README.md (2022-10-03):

# Analyse fonctionnelle

Nous avons rassemblé ici, toutes les contraintes auxquelles devrait répondre le robot, ainsi que toutes les fonctionnalité qu'il devrait posséder dans sa première version.

⚠️ Cette liste est non exhaustive est à de grande chance d'évoluer pendant la durée du projet. ⚠️

Dans le schéma suivant:

* **FP** : correspond à fonction principale.
* **FS** : correspond à fonction secondaire.
* **FC** : correspond à fonction contrainte.
## Cahier des charges

| Fonction | Rôle |
| --- | --- |
| FP1 | Le robot doit pouvoir saisir des canettes |
| FP2 | Le robot doit pouvoir se déplacer |
| FP3 | Le robot doit pouvoir se localiser|
| FP4 | Le robot doit pouvoir identifier des objets|
|||
| FS1.1 | Le robot doit pouvoir détecter les couleurs|
| FS1.2| Le robot doit pouvoir soulever la canette|
| FS1.3| Le robot doit pouvoir relâcher la canette|
| FS2.1| Le robot doit pouvoir retourner à la zone de dépôt|
| FS3.1 | Le robot doit pouvoir détecter les bordures|
| FS3.2| Le robot ne doit pas tomber de la table|
| FS4.1| Le robot doit pouvoir éviter les obstacles|
| FS4.2| Le robot doit pouvoir identifier la zone de dépôt|
|||
|FC1.1| Le robot doit avoir des pinces de la bonne dimension|
| FC2.1| Le robot doit évoluer dans une zone prédéfinie|
| FC2.2| Le robot doit réaliser le parcours en roulant le plus rapidement possible|
| FC3.1| Le robot doit être autonome|
| FC3.2| Le robot ne doit pas passer au même endroit |
| FC3.3| Connaître exactement la distance parcourue par le robot|
| FC4.1| Le robot doit avoir une zone de dépôt|
| FC4.2| Le robot doit pouvoir distinguer un obstacle d'une canette|

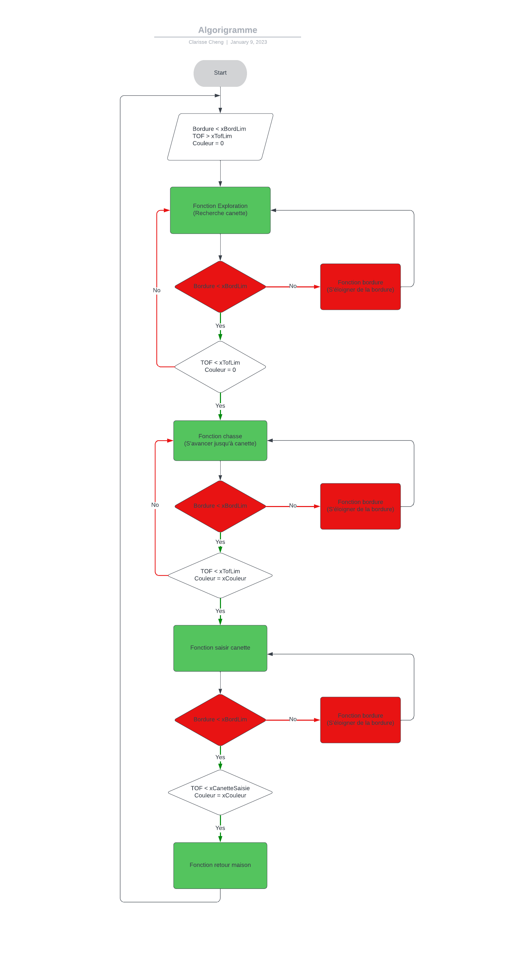
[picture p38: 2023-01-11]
Diagramme/Algorigramme.png

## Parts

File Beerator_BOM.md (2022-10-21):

# Bill of material

### List of components

|Source: |/Users/arthurpellegrin/Desktop/Beerator-2/Beerator.kicad_sch |FIELD3 |FIELD4 |FIELD5 |FIELD6 |FIELD7|
|---|---|---|---|---|---|---|
|Date: |2022 October 21, Friday 13:42:38 | | | | | |
|Tool: |Eeschema (6.0.7-1)-1 | | | | | |
|Generator: |/Applications/KiCad/KiCad.app/Contents/SharedSupport/plugins/bom_csv_grouped_by_value_with_fp.py| | | | | |
|Component Count: |71 | | | | | |
|Ref |Qnty |Value |Cmp name |Footprint |Description |Vendor|
|C102, |1 |22uF |C_Small |Capacitor_SMD:C_0603_1608Metric_Pad1.08x0.95mm_HandSolder |Unpolarized capacitor, small symbol | |
|C201, C202,C101, |3 |10µF |C_Small |Capacitor_THT:CP_Radial_D5.0mm_P2.00mm |Unpolarized capacitor, small symbol | |
|C203, C207, C208, C209, C210, |5 |0.1uF |C_Small |Capacitor_SMD:C_0603_1608Metric_Pad1.08x0.95mm_HandSolder |Unpolarized capacitor, small symbol | |
|C204, C205,C103, C104, |4 |1µF |C_Small |Capacitor_SMD:C_0603_1608Metric_Pad1.08x0.95mm_HandSolder |Unpolarized capacitor, small symbol | |
|C206, |1 |100uF |C_Polarized_Small_US |Capacitor_THT:CP_Radial_D5.0mm_P2.00mm |Polarized capacitor, small US symbol | |
|C401, C402, |2 |15p |C_Small |Capacitor_SMD:C_0603_1608Metric_Pad1.08x0.95mm_HandSolder |Unpolarized capacitor, small symbol | |
|C403, |1 |100n |C_Small |Capacitor_SMD:C_0603_1608Metric_Pad1.08x0.95mm_HandSolder |Unpolarized capacitor, small symbol | |
|C404, |1 |4,7u |C_Small |Capacitor_THT:CP_Radial_D5.0mm_P2.00mm |Unpolarized capacitor, small symbol | |
|D101, D102, |2 |LED_Small |LED_Small |LED_SMD:LED_0603_1608Metric_Pad1.05x0.95mm_HandSolder |Light emitting diode, small symbol | |
|H101, H102, H103, H104, |4 |MountingHole_Pad |MountingHole_Pad |MountingHole:MountingHole_3.2mm_M3_Pad_Via |Mounting Hole with connection | |
|JBat1, |1 |Conn_01x02_Female |Conn_01x02_Female |Connector_JST:JST_XH_B2B-XH-AM_1x02_P2.50mm_Vertical |Generic connector, single row, 01x02, script generated (kicad-library-utils/schlib/autogen/connector/) | |
|JCOLOR0,JCOLOR1, |2 |Conn_01x07_Female |Conn_01x07_Female |Connector_JST:JST_XH_B7B-XH-AM_1x07_P2.50mm_Vertical |Generic connector, single row, 01x07, script generated (kicad-library-utils/schlib/autogen/connector/) | |
|JDistance0_1, JDistance0_2,JDistance1_1, JDistance1_2,JSERVO0,JSERVO1,|6 |Conn_01x03_Female |Conn_01x03_Female |Connector_JST:JST_XH_B3B-XH-AM_1x03_P2.50mm_Vertical |Generic connector, single row, 01x03, script generated (kicad-library-utils/schlib/autogen/connector/) | |
|JMCC2_0,JMCC1_0,JMCC1_1,JMCC2_1,JTOF0_0,JTOF0_1,JTOF1_0,JTOF1_1, |8 |Conn_01x06_Female |Conn_01x06_Female |Connector_JST:JST_XH_B6B-XH-AM_1x06_P2.50mm_Vertical |Generic connector, single row, 01x06, script generated (kicad-library-utils/schlib/autogen/connector/) | |
|JP1, JP2, JP3, JP4, JP5, JP6, |6 |SolderJumper_2_Open |SolderJumper_2_Open |Jumper:SolderJumper-3_P2.0mm_Open_TrianglePad1.0x1.5mm |Solder Jumper, 2-pole, open | |
|JSTLINK1, |1 |Conn_02x07_Odd_Even |Conn_02x07_Odd_Even |Connector_PinHeader_1.27mm:PinHeader_2x07_P1.27mm_Vertical_SMD|Generic connector, double row, 02x07, odd/even pin numbering scheme (row 1 odd numbers, row 2 even numbers), script generated (kicad-library-utils/schlib/autogen/connector/)| |
|R103, R105, |2 |215 |R_Small |Resistor_SMD:R_0603_1608Metric_Pad0.98x0.95mm_HandSolder |Resistor, small symbol | |
|R205, |1 |10k |R_Small |Resistor_SMD:R_0603_1608Metric_Pad0.98x0.95mm_HandSolder |Resistor, small symbol | |
|R301, R302, R303, R304, |4 |1k |R_Small |Resistor_SMD:R_0603_1608Metric_Pad0.98x0.95mm_HandSolder |Resistor, small symbol | |
|R401, |1 |80 |R_Small |Resistor_SMD:R_0603_1608Metric_Pad0.98x0.95mm_HandSolder |Resistor, small symbol | |
|REG3-3, |1 |MCP1802x-xx02xOT |MCP1802x-xx02xOT |Package_TO_SOT_SMD:SOT-23-5 |150mA, Tiny CMOS LDO With Shutdown, Fixed Voltage, SOT-23-5 | |
|REG5, |1 |AZ1117-5.0 |AZ1117-5.0 |Package_TO_SOT_SMD:SOT-223 |1A 20V Fixed LDO Linear Regulator, 5.0V, SOT-89/SOT-223/TO-220/TO-252/TO-263 | |
|SW1, |1 |SW_DPDT_x2 |SW_DPDT_x2 |SamacSys_Parts:NE555DR |Switch, dual pole double throw, separate symbols | |
|U5, |1 |Servo |Servo | | | |
|UColor0, |1 |Color-sensor-TCS3200 |Color-sensor-TCS3200 | | | |
|UDistance1, UDistance2, |2 |Distance-Sensor-GP2Y0D805Z0F|Distance-Sensor-GP2Y0D805Z0F| | | |
|UDRIVER1, UDRIVER2, |2 |ZXBM5210-S |ZXBM5210-S |Package_SO:SOIC-8_3.9x4.9mm_P1.27mm |Reversible DC motor drive with speed control, 3-18V, 0.85A, SOIC-8 | |
|UMCC1, UMCC2, |2 |FIT0521 |FIT0521 | | | |
|USTM1, |1 |STM32G070RBT6 |STM32G070RBT6 |Package_QFP:LQFP-64-1EP_10x10mm_P0.5mm_EP6.5x6.5mm | | |
|UTOF0, UTOF1, |2 |TOF-SENSOR-VL53LX |TOF-SENSOR-VL53LX | | | |
|Y401, |1 |16MHz |Crystal_Small |Crystal:Crystal_SMD_0603-4Pin_6.0x3.5mm |Two pin crystal, small symbol | |

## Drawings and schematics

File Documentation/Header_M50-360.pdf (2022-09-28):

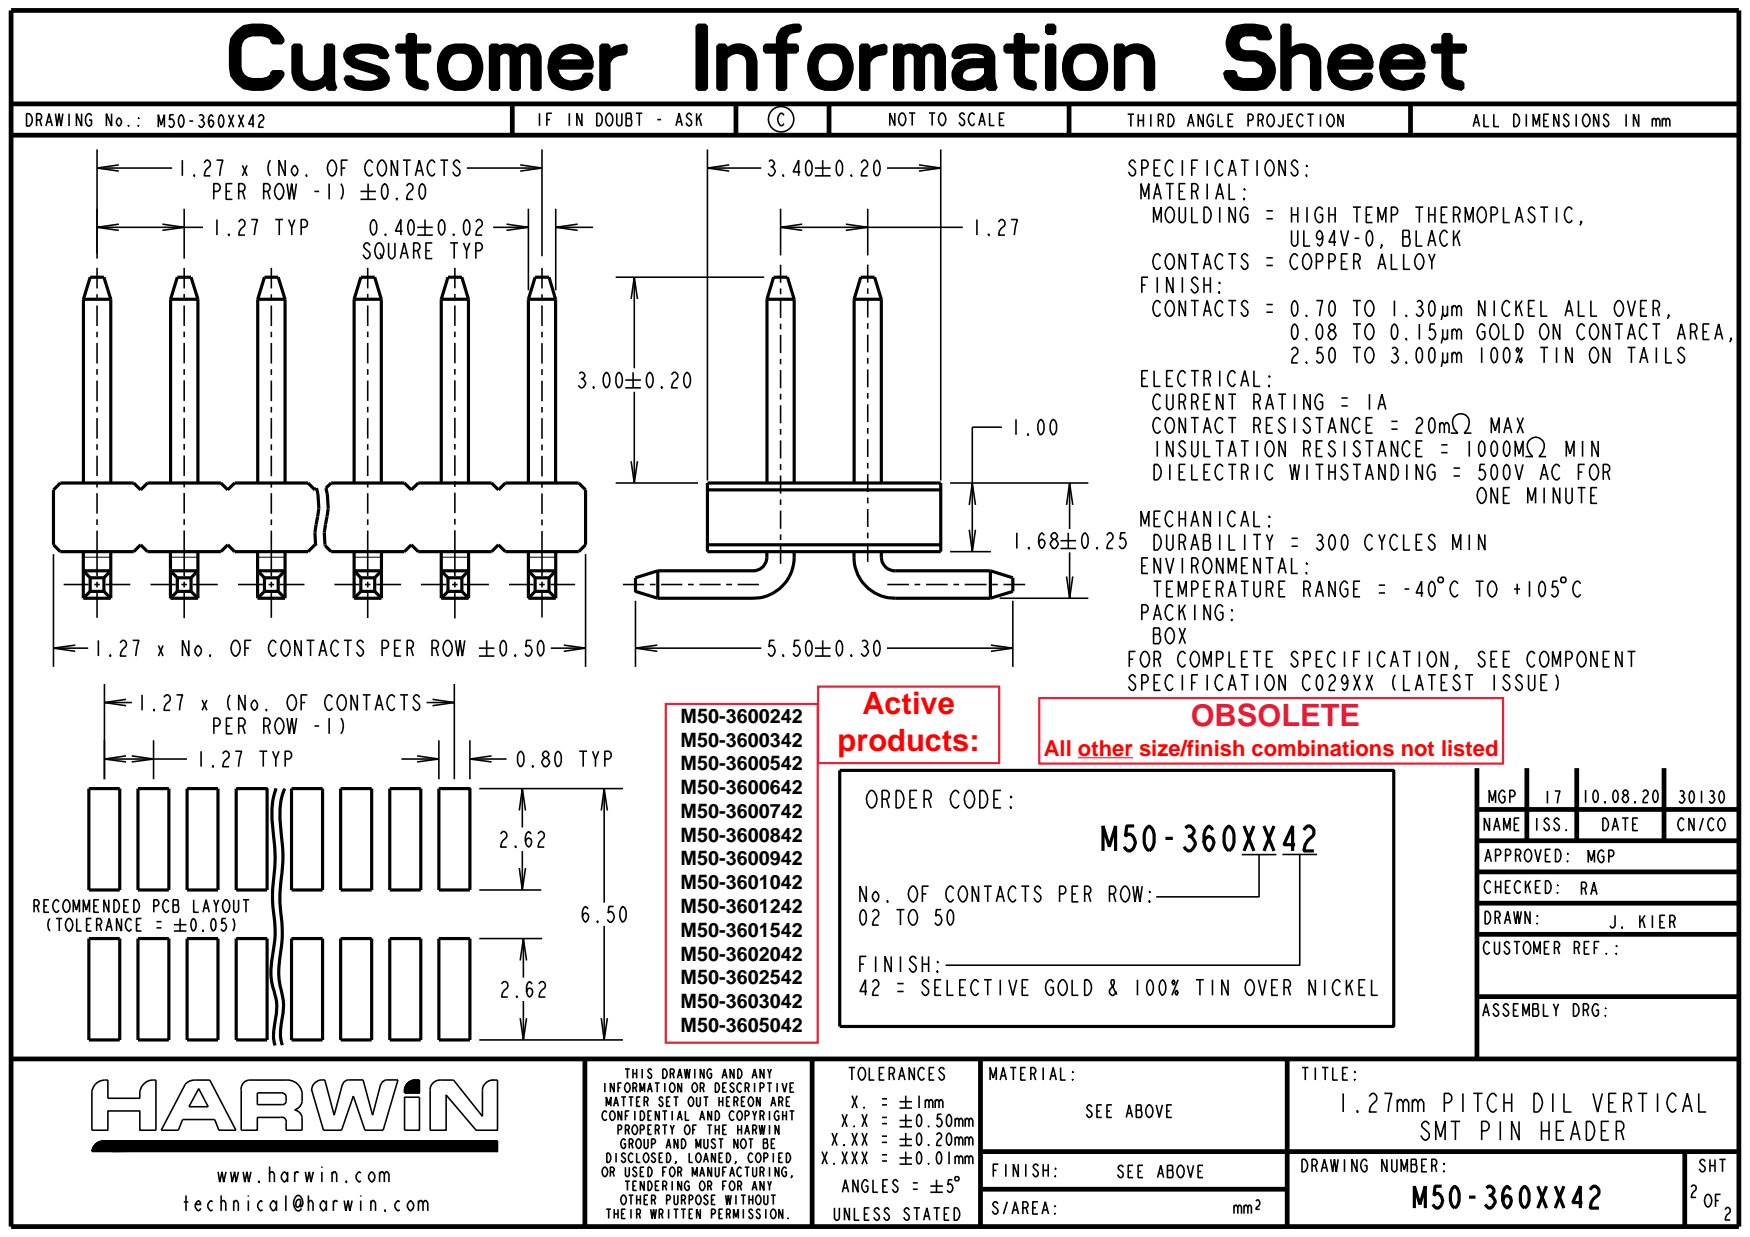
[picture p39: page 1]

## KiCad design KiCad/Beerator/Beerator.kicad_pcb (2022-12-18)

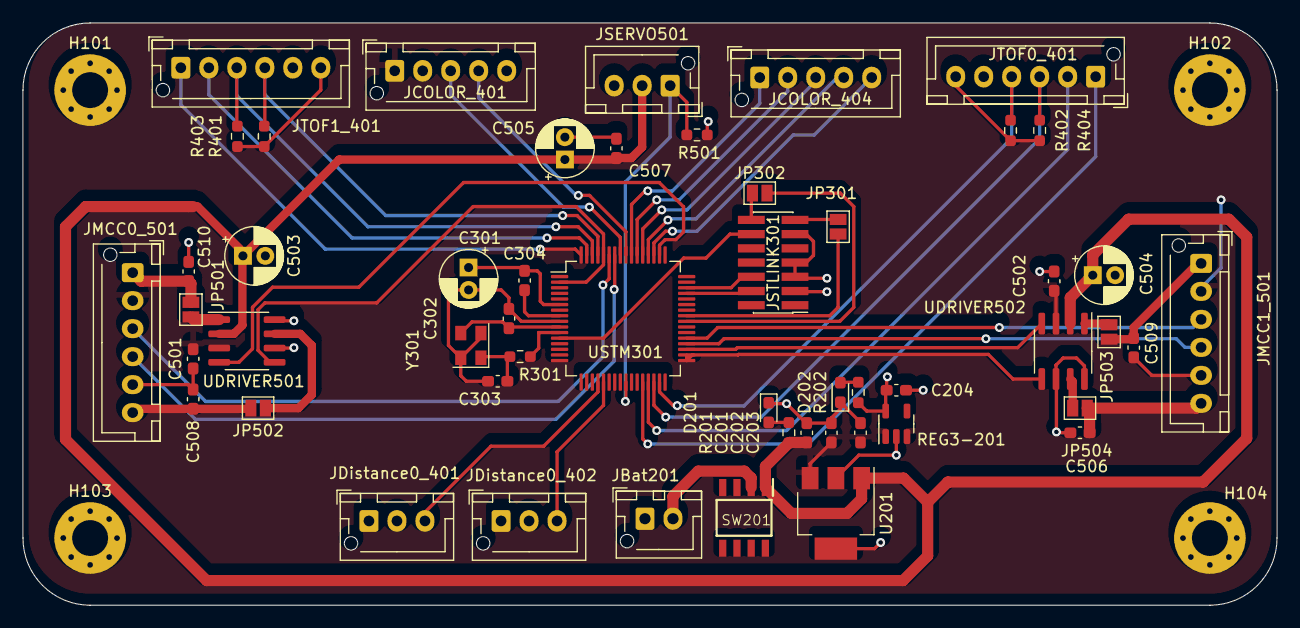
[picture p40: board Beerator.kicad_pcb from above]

Board: 4 copper layers, 112.0 x 52.0 mm, 56 parts (0 on the bottom side), 52 nets.

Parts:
C201: 10uF; C_0603_1608Metric_Pad1.08x0.95mm_HandSolder
C202: 22uF; C_0603_1608Metric_Pad1.08x0.95mm_HandSolder
C203, C204: 1uF; C_0603_1608Metric_Pad1.08x0.95mm_HandSolder
C301: 4,7u; CP_Radial_D5.0mm_P2.00mm
C302, C303: 15p; C_0603_1608Metric_Pad1.08x0.95mm_HandSolder
C304: 100n; C_0603_1608Metric_Pad1.08x0.95mm_HandSolder
C501, C502: 1µF; C_0603_1608Metric_Pad1.08x0.95mm_HandSolder
C503, C504: 10µF; CP_Radial_D5.0mm_P2.00mm
C505: 100uF; CP_Radial_D5.0mm_P2.00mm
C506, C507, C508, C509, C510: 0.1uF; C_0603_1608Metric_Pad1.08x0.95mm_HandSolder
D201, D202: LED_Small; LED_0603_1608Metric_Pad1.05x0.95mm_HandSolder
H101, H102, H103, H104: MountingHole_Pad; MountingHole_3.2mm_M3_Pad_Via
JBat201: Conn_01x02_Female; JST_XH_B2B-XH-AM_1x02_P2.50mm_Vertical
JCOLOR_401, JCOLOR_404: Conn_01x05_Female; JST_XH_B5B-XH-AM_1x05_P2.50mm_Vertical
JDistance0_401, JDistance0_402: Conn_01x03_Female; JST_XH_B3B-XH-AM_1x03_P2.50mm_Vertical
JMCC0_501, JMCC1_501: Conn_01x06_Female; JST_XH_B6B-XH-AM_1x06_P2.50mm_Vertical
JP301, JP302, JP501, JP502, JP503, JP504: SolderJumper_2_Open; SolderJumper-2_P1.3mm_Open_Pad1.0x1.5mm
JSERVO501: Conn_01x03_Female; JST_XH_B3B-XH-AM_1x03_P2.50mm_Vertical
JSTLINK301: Conn_02x07_Odd_Even; PinHeader_2x07_P1.27mm_Vertical_SMD
JTOF0_401, JTOF1_401: Conn_01x06_Female; JST_XH_B6B-XH-AM_1x06_P2.50mm_Vertical
R201: 4,2k; R_0603_1608Metric_Pad0.98x0.95mm_HandSolder
R202: 300; R_0603_1608Metric_Pad0.98x0.95mm_HandSolder
R301: 80; R_0603_1608Metric_Pad0.98x0.95mm_HandSolder
R401, R402, R403, R404: 1k; R_0603_1608Metric_Pad0.98x0.95mm_HandSolder
R501: 10k; R_0603_1608Metric_Pad0.98x0.95mm_HandSolder
REG3-201: MCP1802x-xx02xOT; SOT-23-5
SW201: SW_DPDT_x2; NE555DR
U201: REG-5; SOT-223
UDRIVER501, UDRIVER502: ZXBM5210-S; SOIC-8_3.9x4.9mm_P1.27mm
USTM301: STM32G070RBT6; LQFP-64_10x10mm_P0.5mm
Y301: Crystal_GND23; Crystal_SMD_EuroQuartz_MT-4Pin_3.2x2.5mm

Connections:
+3.3V: C204.1, C301.1, C304.1, JDistance0_401.2, JDistance0_402.2, JSTLINK301.3, JTOF0_401.6, JTOF1_401.6, R202.1, R401.1, R402.2, R403.2, R404.1, R501.2, REG3-201.5 (VOUT), USTM301.6 (VBAT)
+5V: C202.1, C203.1, C501.2, C502.2, JCOLOR_401.1, JMCC0_501.2, JMCC1_501.2, REG3-201.1 (VIN), REG3-201.3 (~SHDN), U201.3 (OUT), UDRIVER501.3 (VDD), UDRIVER502.3 (VDD)
+BATT: C201.1, C503.1, C504.1, C505.1, C507.2, JSERVO501.2, R201.1, SW201.1 (A), U201.1 (Vin), UDRIVER501.2 (VM), UDRIVER502.2 (VM)
/Control/RX_JP: JP301.2 (B), JSTLINK301.13
/Control/TX_JP: JP302.1 (A), JSTLINK301.14
GND: C201.2, C202.2, C203.2, C204.2, C301.2, C302.2, C303.1, C501.1, C502.1, C503.2, C504.2, C505.2, C506.1, C507.1, C508.1, C509.1, C510.1, D201.1 (K), D202.1 (K), H101.1, H102.1, H103.1, H104.1, JBat201.1, JCOLOR_401.2, JCOLOR_401.5, JDistance0_401.1, JDistance0_402.1, JMCC0_501.5, JMCC1_501.5, JSERVO501.3, JSTLINK301.5, JSTLINK301.7, JSTLINK301.11, JTOF0_401.5, JTOF1_401.5, REG3-201.2 (GND), U201.2 (GND), U201.4 (GND), UDRIVER501.6 (VREF), UDRIVER501.8 (GND), UDRIVER502.6 (VREF), UDRIVER502.8 (GND), USTM301.9 (VSS/VSSA), Y301.2, Y301.4
IR1-OUT: JDistance0_402.3, USTM301.21 (PA4/GPIO_EXTI4)
IR2-OUT: JDistance0_401.3, USTM301.20 (PA3/GPIO_EXTI3)
NPWM_D1: UDRIVER501.5 (REV), USTM301.2 (PC12/TIM14_CH1/PWM), USTM301.60 (PB6/PWM/TIM16_CH1N)
NPWM_D2: UDRIVER502.5 (REV), USTM301.33 (PB13/TIM15_CH1N/PWM), USTM301.34 (PB14/TIM15_CH1/PWM)
NRST: JSTLINK301.12, USTM301.12 (NRST)
unnamed: C302.1, USTM301.10 (PF0-OSC_IN), Y301.3
unnamed: C303.2, R301.1, Y301.1
unnamed: C304.2, USTM301.8 (VDD/VDDA)
unnamed: D201.2 (A), R201.2
unnamed: D202.2 (A), R202.2
unnamed: JBat201.2, SW201.2 (B)
unnamed: JP501.1 (A), UDRIVER501.1 (OUT1)
unnamed: JP502.1 (A), UDRIVER501.7 (OUT2)
unnamed: JP503.1 (A), UDRIVER502.1 (OUT1)
unnamed: JP504.1 (A), UDRIVER502.7 (OUT2)
unnamed: R301.2, USTM301.11 (PF1-OSC_OUT)
O1_D1: C510.2, JMCC0_501.1, JP501.2 (B)
O1_D2: C509.2, JMCC1_501.1, JP503.2 (B)
O2_D1: C508.2, JMCC0_501.6, JP502.2 (B)
O2_D2: C506.2, JMCC1_501.6, JP504.2 (B)
PHASE_A_M1: JMCC0_501.4, USTM301.58 (PB4/TIM3_CH1/EncoderMode)
PHASE_A_M2: JMCC1_501.4, USTM301.36 (PA8/TIM1_CH1/EncoderMode)
PHASE_B_M1: JMCC0_501.3, USTM301.59 (PB5/TIM3_CH2/EncoderMode)
PHASE_B_M2: JMCC1_501.3, USTM301.37 (PA9/TIM1_CH2/EncoderMode)
PWM_D1: UDRIVER501.4 (FWD), USTM301.50 (PD0/TIM16_CH1/PWM)
PWM_D2: UDRIVER502.4 (FWD), USTM301.35 (PB15/TIM15_CH2/PWM)
RX: JP301.1 (A), USTM301.41 (PD9/USART3_RX)
SERVO_DATA: JSERVO501.1, R501.1, USTM301.25 (PC4/USART1_TX/Single_Wire)
SWCLK: JSTLINK301.6, USTM301.46 (PA14-BOOT0/SYS_SWCLK/)
SWDIO: JSTLINK301.4, USTM301.45 (PA13/SYS_SWDIO/)
TCS-LED: JCOLOR_401.4, USTM301.56 (PD6/GPIO_Output)
TCS-OE: JCOLOR_401.3, USTM301.57 (PB3/GPIO_Output)
TCS-OUT: JCOLOR_404.5, USTM301.51 (PD1/TIM17_CH1/Input_Capture)
TCS-S0: JCOLOR_404.1, USTM301.55 (PD5/GPIO_Outpur)
TCS-S1: JCOLOR_404.2, USTM301.54 (PD4/GPIO_Output)
TCS-S2: JCOLOR_404.3, USTM301.53 (PD3/GPIO_Output)
TCS-S3: JCOLOR_404.4, USTM301.52 (PD2/GPIO_Output)
TOF2_EXTI: JTOF1_401.1, USTM301.64 (PC10/GPIO_EXTI10)
TOF2_SCL: JTOF1_401.3, R403.1, USTM301.62 (PB8/I2C1_SCL)
TOF2_SDA: JTOF1_401.4, R401.2, USTM301.61 (PB7/I2C1_SDA)
TOF2_XSHUT: JTOF1_401.2, USTM301.63 (PB9/GPIO_OutPut)
TOF-EXTI: JTOF0_401.1, USTM301.28 (PB1/GPIO_EXTI1)
TOF-SCL: JTOF0_401.3, R404.2, USTM301.30 (PB10/I2C2_SCL)
TOF-SDA: JTOF0_401.4, R402.1, USTM301.31 (PB11/I2C2_SDA)
TOF-XSHUT: JTOF0_401.2, USTM301.29 (PB2/GPIO_OUTPUT)
TX: JP302.2 (B), USTM301.40 (PD8/USART3_TX)

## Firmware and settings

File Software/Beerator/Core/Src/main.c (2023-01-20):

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
/* Includes ------------------------------------------------------------------*/
#include "main.h"
#include "cmsis_os.h"
#include "adc.h"
#include "i2c.h"
#include "tim.h"
#include "usart.h"
#include "gpio.h"

/* USER CODE BEGIN Includes */
#include <stdio.h>
#include <stdlib.h>
#include <string.h>

#include "motor_drive.h"
#include "shell.h"
#include "drv_uart1.h"
#include "XL320.h"
#include "asserv.h"
#include "tof.h"
/* USER CODE END Includes */

/* USER CODE BEGIN PD */
#define STACK_SIZE 300
#define ANGLE_ERROR 5
/* USER CODE END PD */

/* USER CODE BEGIN PM */
char * logo = "\r\n\n\n .oPYo. .oPYo. .oPYo.  .oPYo.      .oo ooooo .oPYo.  .oPYo.\r\n8   `8 8.     8.      8   `8     .P 8   8   8    8  8   `8\r\no8YooP' `boo   `boo   o8YooP'    .P  8   8   8    8 o8YooP'\r\n 8   `b .P     .P      8   `b   oPooo8   8   8    8  8   `b\r\n8    8 8      8       8    8  .P    8   8   8    8  8    8\r\n8oooP' `YooP' `YooP'  8    8 .P     8   8   `YooP'  8    8\r\n:......::.....::.....::..:::....:::::..::..:::.....::..:::..\r\n::::::::::::::::::::::::::::::::::::::::::::::::::::::::::::\r\n::::::::::::::::::::::::::::::::::::::::::::::::::::::::::::\r\n\r\n\r\n\r\n";

/* USER CODE END PM */


/* USER CODE BEGIN PV */

//Shell
h_shell_t h_shell;

// Motors
h_motor_t motor1;
h_motor_t motor2;
h_motors_t motors;
pos_R pos;

// Servo
h_XL320_t XL320;

//TOF
TOF_InitStruct tof;

//parametre Robot

float angle;
float distance;
int mesure ;


//Handlers

TaskHandle_t xOpenXL320Handle = NULL;
TaskHandle_t xCloseXL320Handle = NULL;
TaskHandle_t xBorderDetectionHandle = NULL;
TaskHandle_t xMotorSpeedControl = NULL;
TaskHandle_t xTOFMesure = NULL;
TaskHandle_t xTurnHandle = NULL;
TaskHandle_t xTurnReverseRightHandle = NULL;
TaskHandle_t xTurnReverseLeftHandle = NULL;
TaskHandle_t  xGetPosHandle=NULL;
TaskHandle_t xAvanceHandle=NULL;
TaskHandle_t xBackHandle=NULL;
TaskHandle_t xSearchHandle=NULL;



//Global

float distance = 100;
int borderDetected = 0;
/* USER CODE END PV */

void SystemClock_Config(void);
void MX_FREERTOS_Init(void);
/* USER CODE BEGIN 0 */
int __io_putchar(int chr)
{
	HAL_UART_Transmit(&UART_DEVICE, (uint8_t*)&chr, 1, HAL_MAX_DELAY);
	return chr;
}



// Task

void Start_Shell(void* pvParameters){
	shell_run(&h_shell);
	vTaskDelete(NULL);
}

void Motor_Speed_Control(void * PvParameters){
	motor2.htim_motor->Instance->CCR1 = 20;
	motor1.htim_motor->Instance->CCR1 = 20;
	xTaskNotifyGive(xSearchHandle);
	for(;;){
		pid_vitesse(&motor2);
		pid_vitesse(&motor1);
		vTaskDelay(100);
	}
	vTaskDelete(NULL);
}

void Get_Position(void*PvParameters)
{
	for(;;)
	{
		update_position(&pos, &motor1);
		update_position(&pos, &motor2);
		vTaskDelay(50);
	}
	vTaskDelete(NULL);
}


void Border_Detected(void * PvParameters){
	float angle=35;
	for(;;){
		ulTaskNotifyTake(pdTRUE, portMAX_DELAY);
		motor_stop(&motor2);
		motor_stop(&motor1);
		float buff_r = pos.dR;
		float buff_l = pos.dL;

		motor_run_reverse(&motor1);
		motor_run_reverse(&motor2);

		while((abs(buff_r - pos.dR) < 100) && (abs(buff_l - pos.dL) < 100))
		{
			if(abs(buff_r - pos.dR) > 100){
				motor_stop(&motor1);

			}
			if(abs(buff_l - pos.dL) > 100){
				motor_stop(&motor2);

			}
		}
		motor_stop(&motor1);
		motor_stop(&motor2);

		float buff=pos.alpha;
		motor_run_reverse(&motor2);
		while(abs(angle-abs(buff-pos.alpha))>ANGLE_ERROR)
		{

		}
		motor_stop(&motor2);

		borderDetected = 0 ;
		printf("Border Avoided \r\n");

		mesure = 0;
		xTaskNotifyGive(xAvanceHandle);
	}
	vTaskDelete(NULL);
}

void Search_Task(void* PvParameters){
	for(;;){
		ulTaskNotifyTake(pdTRUE, portMAX_DELAY);
		printf("Search Task \r\n");
		int delay = rand() % 5000;
		motor_stop(&motor2);
		motor_stop(&motor1);
		motor2.speedInstruction =  50;
		motor_run_forward(&motor2);
		vTaskDelay(delay);
		motor2.speedInstruction =  SPEED_COMMAND;

		motor_run_forward(&motor1);
	}
	vTaskDelete(NULL);
}

void TOF_Task(void* PvParameters){
	for(;;){
		mesure = TOF_measure();
		if((mesure != -1) && (mesure > 30)){
			motor_stop(&motor1);
			motor_stop(&motor2);
			xTaskNotifyGive(xOpenXL320Handle);
			xTaskNotifyGive(xAvanceHandle);
		}
		if((mesure != -1) && (mesure < 30)){
			motor_stop(&motor1);
			motor_stop(&motor2);
			xTaskNotifyGive(xCloseXL320Handle);
		}
		vTaskDelay(100);
	}
}

void Avance_Task(void*PvParameters)
{
	for(;;)
	{
		ulTaskNotifyTake(pdTRUE, portMAX_DELAY);
		printf("Advanced Task \r\n");
		float buff_r = pos.dR;
		float buff_l = pos.dL;
		motor_run_forward(&motor1);
		motor_run_forward(&motor2);
		while((abs(buff_r - pos.dR) < mesure) && (abs(buff_l - pos.dL) < mesure))
		{
			if(abs(buff_r - pos.dR) > mesure){
				motor_stop(&motor1);

			}
			if(abs(buff_l - pos.dL) > mesure){
				motor_stop(&motor2);

			}
		}
		motor_stop(&motor2);
		motor_stop(&motor1);
		xTaskNotifyGive(xSearchHandle);
	}
	vTaskDelete(NULL);
}

void XL320_Open(void * pvParameterts){
	for(;;){
		ulTaskNotifyTake(pdTRUE, portMAX_DELAY);
		printf("OPEN PINCE \r\n");

		if(XL320_set_goal_position(&XL320, XL320_OPEN_ANGLE) != XL320_OK){
			printf("Error Opening XL320 \r\n");
		};
	}
	vTaskDelete(NULL);
}

void XL320_Catch_Task(void * pvParameterts){
	for(;;){
		ulTaskNotifyTake(pdTRUE, portMAX_DELAY);
		printf("Close Pince \r\n");

		uint16_t XL320_Response = XL320_Catch(&XL320);
		if(XL320_Response == XL320_ERROR){
			printf("Error Catching XL320 \r\n");
		}
	}
	vTaskDelete(NULL);
}
// Shell Function Text

int XL320_Open_Shell(h_shell_t * h_shell, int argc, char ** argv)
{
	xTaskNotifyGive(xOpenXL320Handle);
	return SHELL_OK;
}

int XL320_Catch_Shell(h_shell_t * h_shell, int argc, char ** argv)
{
	xTaskNotifyGive(xCloseXL320Handle);
	return SHELL_OK;
}

int Avance_shell()
{
	xTaskNotifyGive(xAvanceHandle);
	return SHELL_OK;
}

int Back_shell()
{
	xTaskNotifyGive(xBackHandle);
	return SHELL_OK;
}

int Turn_shell()
{
	xTaskNotifyGive(xTurnReverseLeftHandle);
	return SHELL_OK;
}

/* USER CODE END 0 */

/**
 * @brief  The application entry point.
 * @retval int
 */
int main(void)
{
	/* MCU Configuration--------------------------------------------------------*/

	/* Reset of all peripherals, Initializes the Flash interface and the Systick. */
	HAL_Init();

	/* Configure the system clock */
	SystemClock_Config();

	/* Initialize all configured peripherals */
	MX_GPIO_Init();
	MX_ADC1_Init();
	MX_TIM1_Init();
	MX_TIM3_Init();
	MX_TIM14_Init();
	MX_TIM16_Init();
	MX_I2C2_Init();
	MX_USART1_UART_Init();
	MX_USART2_UART_Init();
	MX_TIM17_Init();
	/* USER CODE BEGIN 2 */
	printf(logo);

	// Init XL320
	printf("Initialisation XL320 ... \r\n");

	XL320.firmware_version = 0;
	XL320.model_number = 0;
	XL320.uart = &huart2;
	XL320.id = XL320_ID;

	if(XL320_Init(&XL320) != XL320_OK){
		printf("Error Initialising XL320...\r\n");
		Error_Handler();
	};

	printf("Initialisation XL320 Successful \r\n\n");

	printf("Initialisation Motors ... \r\n");

	motor1.htim_motor = MOTOR1_TIM;
	motor1.htim_encoder = ENCODER_MOTOR_1_TIM;
	motor1.htim_encoder->Instance->CNT = motor1.htim_encoder->Instance->ARR / 2;
	motor1.Channel_Motor_Forward = MOTOR1_CHANNEL_FORWARD;
	motor1.Channel_Motor_Reverse = MOTOR1_CHANNEL_REVERSE;
	motor1.counter = motor1.htim_encoder->Instance->ARR / 2;
	motor1.speedInstruction = 0;
	motor1.isReverse = 0;
	motor1.status = MOTOR_PAUSED;

	motor2.htim_motor = MOTOR2_TIM;
	motor2.htim_encoder = ENCODER_MOTOR_2_TIM;
	motor2.htim_encoder->Instance->CNT = motor2.htim_encoder->Instance->ARR / 2;
	motor2.Channel_Motor_Forward = MOTOR2_CHANNEL_FORWARD;
	motor2.Channel_Motor_Reverse = MOTOR2_CHANNEL_REVERSE;
	motor2.counter = motor2.htim_encoder->Instance->ARR / 2;
	motor2.speedInstruction = 0;
	motor2.isReverse = 1;
	motor2.status = MOTOR_PAUSED;

	printf("Initialisation Motor Control ... \r\n");

	HAL_TIM_Encoder_Start_IT(ENCODER_MOTOR_1_TIM, TIM_CHANNEL_ALL);
	HAL_TIM_Encoder_Start_IT(ENCODER_MOTOR_2_TIM, TIM_CHANNEL_ALL);

	pos.dR = 0;
	pos.dL = 0;
	pos.d_alpha = 0;
	pos.alpha = 0;

	printf("Initialisation Motors Successful \r\n\n");

	//TOF
	printf("Initialisation TOF ... \r\n");

	tof.I2cHandle = &hi2c2;
	if(TOF_init(&tof) != 1){
		Error_Handler();
	};

	printf("Initialisation TOF Successful \r\n\n");

	//Shell Configuration
	printf("Launching Shell .... \r\n");
	h_shell.drv.receive = drv_uart1_receive;
	h_shell.drv.transmit = drv_uart1_transmit;
	h_shell.pos = 0;
	h_shell.xHandleShell = NULL;

	shell_init(&h_shell);
	shell_add(&h_shell, 'O', XL320_Open_Shell, "Open XL320");
	shell_add(&h_shell, 'C', XL320_Catch_Shell, "Catch XL320");
	shell_add(&h_shell, 'a', Avance_shell, "Avance ");
	shell_add(&h_shell, 't', Turn_shell, "Recule ");





	// Creating Tasks

	BaseType_t xReturned;

	xReturned = xTaskCreate(Motor_Speed_Control, "SpeedControl", 500, NULL, tskIDLE_PRIORITY + 6, &xMotorSpeedControl);
	if(xReturned != pdPASS){
		printf("Error Creating the task \r\n");
	}
	xReturned = xTaskCreate(Get_Position, "Position", 200, NULL, tskIDLE_PRIORITY + 6, &xGetPosHandle);
	if(xReturned != pdPASS){
		printf("Error Creating the task \r\n");
	}
	xReturned = xTaskCreate(Border_Detected, "Border Detection", 1000, NULL, tskIDLE_PRIORITY + 6 ,&xBorderDetectionHandle);
	if(xReturned != pdPASS){
		printf("Error Creating the task \r\n");
	}

	xReturned = xTaskCreate(Avance_Task, "Avance Task", 500, NULL, tskIDLE_PRIORITY + 5, &xAvanceHandle);
	if(xReturned != pdPASS){
		printf("Error Creating the task \r\n");
	}

	xReturned = xTaskCreate(TOF_Task, "TOFMesure", 1000, NULL, tskIDLE_PRIORITY + 4, &xTOFMesure);
	if(xReturned != pdPASS){
		printf("Error Creating the task \r\n");
	}

	xReturned = xTaskCreate(Search_Task, "Search Task", 100, NULL, tskIDLE_PRIORITY + 2, &xSearchHandle);
	if(xReturned != pdPASS){
		printf("Error Creating the task \r\n");
	}


	xReturned = xTaskCreate(Start_Shell, "StartShell", STACK_SIZE, NULL, tskIDLE_PRIORITY, &h_shell.xHandleShell);
	if(xReturned != pdPASS){
		printf("Error Creating the task \r\n");
	}


	xReturned = xTaskCreate(XL320_Catch_Task, "XL320_Close", STACK_SIZE, NULL, tskIDLE_PRIORITY + 5 ,&xCloseXL320Handle);
	if(xReturned != pdPASS){
		printf("Error Creating the task \r\n");
	}

	xReturned = xTaskCreate(XL320_Open, "XL320_OPEN", STACK_SIZE, NULL, tskIDLE_PRIORITY + 5,&xOpenXL320Handle);
	if(xReturned != pdPASS){
		printf("Error Creating the task \r\n");
	}



	vTaskStartScheduler();
	/* USER CODE END 2 */

	/* Call init function for freertos objects (in freertos.c) */
	MX_FREERTOS_Init();

	/* Start scheduler */
	osKernelStart();

	/* We should never get here as control is now taken by the scheduler */
	/* Infinite loop */
	/* USER CODE BEGIN WHILE */
	while (1)
	{
		/* USER CODE END WHILE */

		/* USER CODE BEGIN 3 */
	}
	/* USER CODE END 3 */
}

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
/* USER CODE BEGIN 4 */
void HAL_UART_RxCpltCallback(UART_HandleTypeDef *huart)
{
	if(huart == &UART_DEVICE){
		BaseType_t xHigherPriorityTaskWoken = pdFALSE;
		vTaskNotifyGiveFromISR(h_shell.xHandleShell, &xHigherPriorityTaskWoken);
		portYIELD_FROM_ISR(xHigherPriorityTaskWoken);
	}

}


void HAL_GPIO_EXTI_Rising_Callback(uint16_t GPIO_Pin){
	if(borderDetected != 1){
		borderDetected = 1;
		BaseType_t xHigherPriorityTaskWoken = pdFALSE;
		if((GPIO_Pin == IR1_OUT_Pin)){
			vTaskNotifyGiveFromISR(xBorderDetectionHandle, &xHigherPriorityTaskWoken);
			portYIELD_FROM_ISR(xHigherPriorityTaskWoken);
		}
		if( (GPIO_Pin == IR2_OUT_Pin)){
			vTaskNotifyGiveFromISR(xBorderDetectionHandle, &xHigherPriorityTaskWoken);
			portYIELD_FROM_ISR(xHigherPriorityTaskWoken);
		}
	}
}

/* USER CODE END 4 */

/**
 * @brief  Period elapsed callback in non blocking mode
 * @note   This function is called  when TIM6 interrupt took place, inside
 * HAL_TIM_IRQHandler(). It makes a direct call to HAL_IncTick() to increment
 * a global variable "uwTick" used as application time base.
 * @param  htim : TIM handle
 * @retval None
 */
void HAL_TIM_PeriodElapsedCallback(TIM_HandleTypeDef *htim)
{
	if (htim->Instance == TIM6) {
		HAL_IncTick();
	}
}

/**
 * @brief  This function is executed in case of error occurrence.
 * @retval None
 */
void Error_Handler(void)
{
	/* USER CODE BEGIN Error_Handler_Debug */
	/* User can add his own implementation to report the HAL error return state */
	__disable_irq();
	while (1)
	{
		HAL_NVIC_SystemReset();
	}
	/* USER CODE END Error_Handler_Debug */
}

#ifdef  USE_FULL_ASSERT
/**
 * @brief  Reports the name of the source file and the source line number
 *         where the assert_param error has occurred.
 * @param  file: pointer to the source file name
 * @param  line: assert_param error line source number
 * @retval None
 */
void assert_failed(uint8_t *file, uint32_t line)
{
	/* USER CODE BEGIN 6 */
	/* User can add his own implementation to report the file name and line number,
     ex: printf("Wrong parameters value: file %s on line %d\r\n", file, line) */
	/* USER CODE END 6 */
}
#endif /* USE_FULL_ASSERT */

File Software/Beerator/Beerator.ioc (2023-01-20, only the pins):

Mcu.UserName=STM32G070RBTx
PA13.Signal=SYS_SWDIO
PA14-BOOT0.Signal=SYS_SWCLK
PA2.GPIO_Label=TOF_INT
PA2.Signal=GPXTI2
PA3.GPIO_Label=TOF_XSHUT
PA3.Signal=GPIO_Output
PA5.GPIO_Label=TOF2_XSHUT
PA5.Signal=GPIO_Output
PB1.GPIO_Label=TCS_OUT
PB1.Signal=S_TIM14_CH1
PB10.GPIO_Label=BAT_SENSE
PB10.Signal=ADC1_IN11
PB13.GPIO_Label=TCS_S3
PB13.Signal=GPIO_Output
PB14.GPIO_Label=TCS_S2
PB14.Signal=GPIO_Output
PB15.GPIO_Label=TCS_LED
PB15.Signal=GPIO_Output
PB4.GPIO_Label=PHASE_B_M2
PB4.Signal=S_TIM3_CH1
PB5.GPIO_Label=PHASE_A_M2
PB5.Signal=S_TIM3_CH2
PB6.GPIO_Label=NPWM_M1
PB6.Signal=TIM16_CH1N
PB7.GPIO_Label=NPWM_M2
PB7.Signal=TIM17_CH1N
PB8.GPIO_Label=PWM_M1
PB8.Signal=S_TIM16_CH1
PB9.GPIO_Label=PWM_M2
PB9.Signal=S_TIM17_CH1
PC11.GPIO_Label=IR1_OUT
PC11.Signal=GPXTI11
PC12.GPIO_Label=IR2_OUT
PC12.Signal=GPXTI12
PC3.GPIO_Label=LED_GREEN
PC3.Signal=GPIO_Output
PC4.Signal=USART1_TX
PC5.Signal=USART1_RX
PC8.GPIO_Label=PHASE_A_M1
PC8.Signal=S_TIM1_CH1
PC9.GPIO_Label=PHASE_B_M1
PC9.Signal=S_TIM1_CH2
PD5.GPIO_Label=SERVO_DATA
PD5.Signal=USART2_TX

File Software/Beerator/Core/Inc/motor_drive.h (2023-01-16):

/*
 * motor_drive.h
 *
 *  Created on: Dec 5, 2022
 *      Author: arthurpellegrin
 */
#include "main.h"
#include "tim.h"

#define ENCODER_MOTOR_1_TIM &htim1
#define ENCODER_MOTOR_2_TIM &htim3

#define MOTOR1_TIM &htim16
#define MOTOR1_CHANNEL_FORWARD TIM_CHANNEL_1
#define MOTOR1_CHANNEL_REVERSE TIM_CHANNEL_1

#define MOTOR2_TIM &htim17
#define MOTOR2_CHANNEL_FORWARD TIM_CHANNEL_1
#define MOTOR2_CHANNEL_REVERSE TIM_CHANNEL_1

#define DEFAULT_PERIOD 100
#define MAX_DUTY 99
#define MIN_DUTY 0

#ifndef INC_MOTOR_DRIVE_H_
#define INC_MOTOR_DRIVE_H_

#endif /* INC_MOTOR_DRIVE_H_ */

typedef enum MOTOR_STATUS {
	MOTOR_FORWARD,
	MOTOR_REVERSE,
	MOTOR_PAUSED,
} MOTOR_STATUS_TYPE;

typedef enum MOTOR_ERRORS {
	MOTOR_NO_CHANGES = 2,
	MOTOR_OK = 1,
	MOTOR_UNKNOWN_ERROR = -1,
	OUT_OF_RANGE = -2,
} MOTOR_ERROR_TYPE;

typedef struct h_motor_t {
	int speedInstruction;
	uint32_t counter;
	int isReverse;
	int vitesse;
	MOTOR_STATUS_TYPE status;
	TIM_HandleTypeDef * htim_motor;
	TIM_HandleTypeDef * htim_encoder;
	uint32_t Channel_Motor_Forward;
	uint32_t Channel_Motor_Reverse;
} h_motor_t;

typedef struct h_motors_t {
	h_motor_t * motor1;
	h_motor_t * motor2;
} h_motors_t;


int motor_run_forward(h_motor_t * motor);

int motor_run_reverse(h_motor_t * motor);

int motor_stop(h_motor_t * motor);

int motor_change_dutyCycle(h_motor_t * motor, int dutyCycle);

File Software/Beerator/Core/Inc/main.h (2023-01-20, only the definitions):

#define IR1_OUT_Pin GPIO_PIN_11
#define IR1_OUT_GPIO_Port GPIOC
#define IR1_OUT_EXTI_IRQn EXTI4_15_IRQn
#define IR2_OUT_Pin GPIO_PIN_12
#define IR2_OUT_GPIO_Port GPIOC
#define IR2_OUT_EXTI_IRQn EXTI4_15_IRQn
#define LED_GREEN_Pin GPIO_PIN_3
#define LED_GREEN_GPIO_Port GPIOC
#define TOF_INT_Pin GPIO_PIN_2
#define TOF_INT_GPIO_Port GPIOA
#define TOF_XSHUT_Pin GPIO_PIN_3
#define TOF_XSHUT_GPIO_Port GPIOA
#define TOF2_XSHUT_Pin GPIO_PIN_5
#define TOF2_XSHUT_GPIO_Port GPIOA
#define TCS_OUT_Pin GPIO_PIN_1
#define TCS_OUT_GPIO_Port GPIOB
#define BAT_SENSE_Pin GPIO_PIN_10
#define BAT_SENSE_GPIO_Port GPIOB
#define TCS_S3_Pin GPIO_PIN_13
#define TCS_S3_GPIO_Port GPIOB
#define TCS_S2_Pin GPIO_PIN_14
#define TCS_S2_GPIO_Port GPIOB
#define TCS_LED_Pin GPIO_PIN_15
#define TCS_LED_GPIO_Port GPIOB
#define TOF_I2C_SCL_Pin GPIO_PIN_11
#define TOF_I2C_SCL_GPIO_Port GPIOA
#define TOF_I2C_SDA_Pin GPIO_PIN_12
#define TOF_I2C_SDA_GPIO_Port GPIOA
#define PHASE_A_M1_Pin GPIO_PIN_8
#define PHASE_A_M1_GPIO_Port GPIOC
#define PHASE_B_M1_Pin GPIO_PIN_9
#define PHASE_B_M1_GPIO_Port GPIOC
#define SERVO_DATA_Pin GPIO_PIN_5
#define SERVO_DATA_GPIO_Port GPIOD
#define PHASE_B_M2_Pin GPIO_PIN_4
#define PHASE_B_M2_GPIO_Port GPIOB
#define PHASE_A_M2_Pin GPIO_PIN_5
#define PHASE_A_M2_GPIO_Port GPIOB
#define NPWM_M1_Pin GPIO_PIN_6
#define NPWM_M1_GPIO_Port GPIOB
#define NPWM_M2_Pin GPIO_PIN_7
#define NPWM_M2_GPIO_Port GPIOB
#define PWM_M1_Pin GPIO_PIN_8
#define PWM_M1_GPIO_Port GPIOB
#define PWM_M2_Pin GPIO_PIN_9
#define PWM_M2_GPIO_Port GPIOB

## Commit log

2022-09-28 Driver Moteur
2022-09-28 Regulateur 3V
2022-09-28 feat(Diagramme + Cahier Des charges)
2022-10-03 Kicad Project
    [BLOC_control.kicad_sch, Beerator.kicad_pcb, Beerator.kicad_sch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]
2022-10-06 feat(Kicad): Schemas V1
    [BLOC_control.kicad_sch, Beerator.kicad_sch, actuator_bloc.kicad_sch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]
2022-10-06 Adding the Beerator's BOM
    The BOM mainly describes the list of components to use, as well as some construction rules/specifications.
2022-10-06 Adding exact references to the BOM
2022-10-08 feat(KiCad): Version 2
    [BLOC_control.kicad_sch, Beerator.kicad_sch, actuator_bloc.kicad_sch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]
2022-10-21 feat(last pcb version)
    [BLOC_control.kicad_sch, Beerator.kicad_pcb, Beerator.kicad_sch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]
2022-10-21 Dimensionement Led
    [alimentation_bloc.kicad_sch]
2022-11-15 Partie Circuit et PCB, sans images
2022-11-15 Ajout illustration partie circuit et PCB
2022-11-15 Ajout illustrations circuit et PCB readme
2022-11-15 Ajout des morceaux de codes
2022-11-16 Correction Carte
    [Beerator.kicad_pcb, actuator_bloc.kicad_sch, sensor_bloc.kicad_sch]
2022-12-01 ADC for battery
2022-12-18 Kicad Changes
    [Beerator.kicad_pcb]
2022-12-18 Beerator new tim config for motors
2023-01-11 pid implementation
2023-01-13 odometrie 13_01

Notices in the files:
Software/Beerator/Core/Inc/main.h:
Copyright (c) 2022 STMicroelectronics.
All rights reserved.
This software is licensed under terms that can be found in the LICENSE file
